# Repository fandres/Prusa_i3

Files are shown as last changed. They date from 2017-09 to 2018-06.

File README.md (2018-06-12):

This repository is possibly outdated
Este Repositorio se probablemente se encuentra desactualizado

Repository migrated to https://gitlab.com/fandres323/Prusa_i3
Repositorio migrado a https://gitlab.com/fandres323/Prusa_i3

# Prusa_i3
============

License 
======

[Creative Commons Attribution-ShareAlike 4.0 International License](http://creativecommons.org/licenses/by-sa/4.0/)

Attributions
============
See commit details to find the authors of each Part.
- @fandres

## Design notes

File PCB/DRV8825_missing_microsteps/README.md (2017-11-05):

## DRV8825 Missing Microsteps
DRV8825 Missing Steps

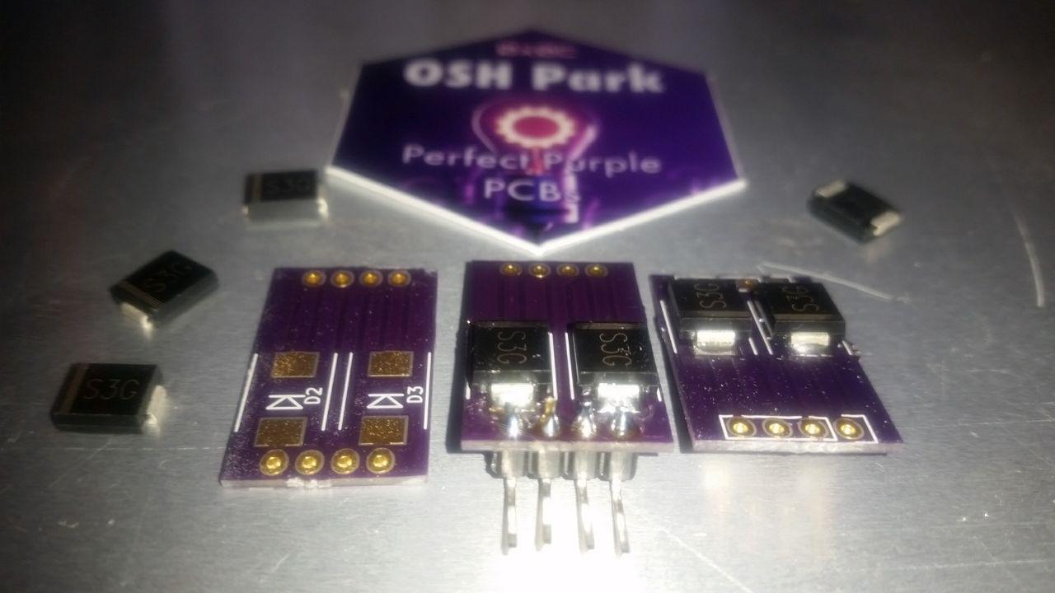
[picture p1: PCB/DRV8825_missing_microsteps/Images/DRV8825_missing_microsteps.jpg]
DRV8825_missing_microsteps


## BOM 
Ref | Qty | Value | Footprint 
--- | --- | ----- | --------
D1 D2 D3 D4  | 4 | S3G SMC DO-214AB 
J1 J2  | 2 | Conn_01x04 

# Order from OSH Park, $3 x2.85 



# Images
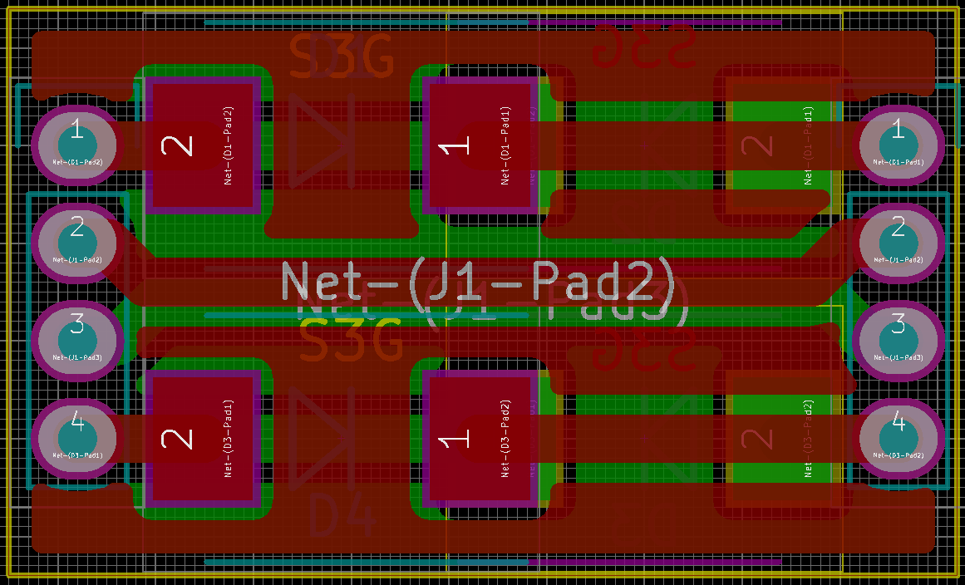
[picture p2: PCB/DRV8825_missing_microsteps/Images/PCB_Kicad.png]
PCB_Kicad


# License 
======

[MIT License](/PCB/DRV8825_missing_microsteps/Images/LICENCE)

# Attributions
============
See commit details to find the authors of each Part.
- @fandres

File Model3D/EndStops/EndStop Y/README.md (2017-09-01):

# Model 3D on FreeCad
============

# Images
3D_

# License 
======

[Creative Commons Attribution-ShareAlike 4.0 International License](http://creativecommons.org/licenses/by-sa/4.0/)

# Attributions
============
Based on the design of by clefranc, Endstop Y Support for Prusa i3 licensed under the Creative Commons - Attribution license. 

See commit details to find the authors of each Part.
- @fandres

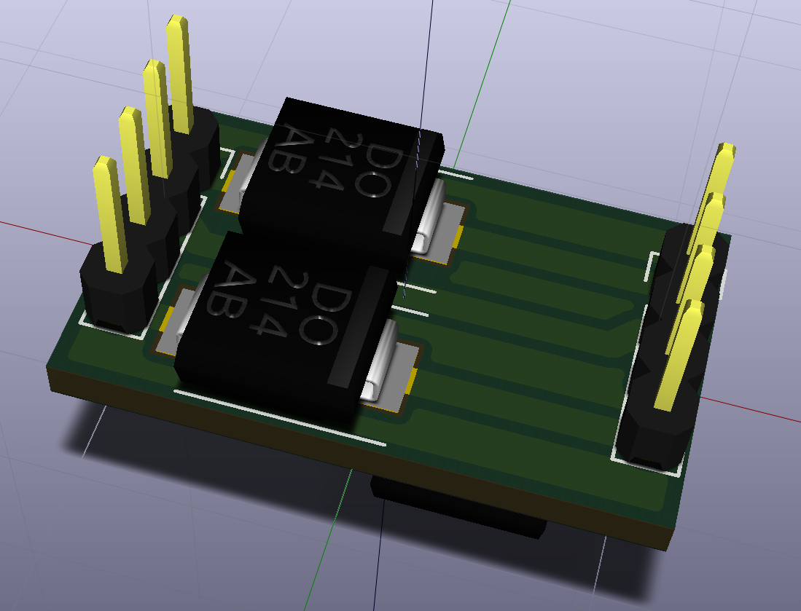
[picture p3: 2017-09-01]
PCB/DRV8825_missing_microsteps/Images/3D_View-F.png

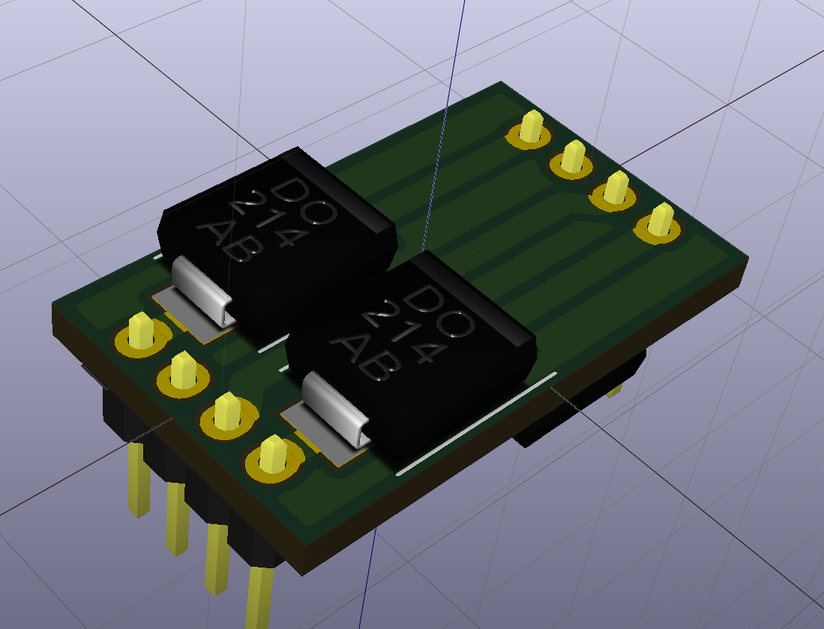
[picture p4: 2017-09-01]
PCB/DRV8825_missing_microsteps/Images/3D_View-B.png

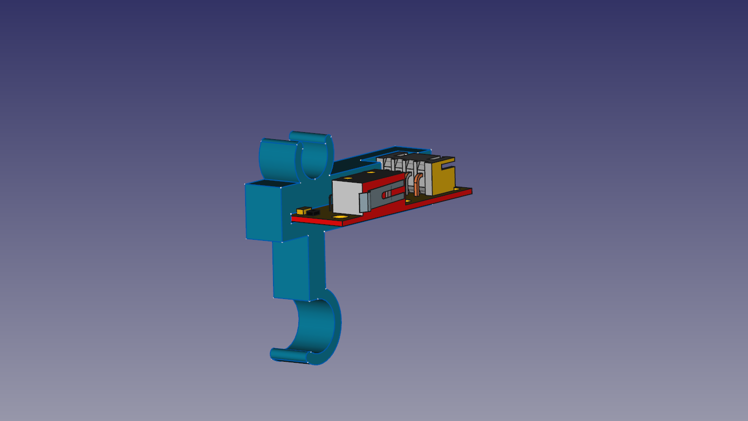
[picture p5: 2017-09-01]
Model3D/EndStops/EndStop Y/Endstop Y.png

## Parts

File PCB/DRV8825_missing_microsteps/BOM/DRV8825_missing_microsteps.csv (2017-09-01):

Title | DRV8825 Missing Microsteps
Revision | 1
Date
Generated | jue 31 ago 2017 22:43:22 -05
Company | Rootdevel
Comment 1 | fAndRes
Comment 2 | CC-4.0 Internacional By
Comment 3
Comment 4
Total Parts | 6
Total Unique Parts | 2
Ref | Qty | Value | Footprint
D1 D2 D3 D4 | 4 | S3G | Diodes_SMD:DO-214AB
J1 J2 | 2 | Conn_01x04 | Pin_Headers:Pin_Header_Straight_1x04
BOM made with KICAD_BOM_WIZARD (https://github.com/HashDefineElectronics/KiCad_BOM_Wizard.git)
Generated jue 31 ago 2017 22:43:22 -05

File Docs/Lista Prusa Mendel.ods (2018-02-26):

 | Estructura |  |  | Electrónica |  | Presupuesto
Cantidad | Elemento |  | Cantidad | Elemento |  | 1.1 | $115.000 | Electrónica básica + DRV8825 Missing
1 | Marco de Aluminio/Acrilico | 4 | 1 | Arduino Mega | 1.1 | 1.2 | $42.000 | Mecánica movimiento
1 | Juego de piezas imprimibles | 5 | 1 | Ramps 1.4 | 1.1 | 2 | $134.100 | Motores
 | Varillas Roscadas | 6 | 1 | HotEnd | 3.1 | 3.1 | $42.000 | Hotend
2 | Métrica 10 (380mm) | 6 | 1 | Cama caliente 200x200mm | 3.3 | 3.2 | $90.000 | Extrusor
4 | Métrica 8 (210mm) | 6 | 5 | Pololu + disipador | 1.1 | 4 | $90.000 | Marco
2 | Métrica 5 (295mm) | 6 | 2 | Termistor de 100K | 3.3 | 5 | $90.000 | Vitaminas + Endstop
 | Varillas Lisas | 6 | 1 | Fuente de alimentación 12v. (al menos de 20A) | 8 | 6 | $80.000 | Estructura: varillas
2 | Métrica 8 (345mm) EJE Y | 6 | 1 | Pantalla LCD (opcional) | 8 | 7 | $109.000 | Tornilleria, Hot-bed y otros
2 | Métrica 8 (320mm) EJE Z | 6 | 3 | Finales de carrera | 5 | 8 | $80.000 | Power Suply + LCD
2 | Métrica 8 (380mm) EJE X | 6 | 3 | Ventilador (electrónica) x2 / x1 Radial | 1.1 | 9 | $83.000 | Filamento
1 | Métrica 8 (20mm) | 6 | 1 | Juego de cableado | 7
 |  |  | 1 | Sensor de proximidad Nivel (Inductivo, BLTouch) | 1.1 |  | Subtotal | 955100
 |  |  | 5 | DRV8825 Missing | 1.1
 | Mecánica
Cantidad | Elemento
5 | Motores NEMA 17 | 2 |  | Tuercas , tornillería y arandelas
2 | Correas GT2 | 1.2 | Cantidad | Elemento
2 | Poleas GT2 | 1.2 |  | Tuercas | 7
10 | Rodamiento LM8UU | 1.2 | 12 | Métrica 10 | 7
2 | Rodamiento 623zz | 1.2 | 24 | Métrica 8 | 7
3 | Rodamiento 608zz | 1.2 | 2 | Métrica 5 | 7
2 | Acoples eje Z | 1.2 | - | Métrica 4 | 7
1 | Tornillo extrusor (hobed bolt) | 3.2 | - | Métrica 3 | 7
4 | Muelle Cama Caliente (20-25mm) | 7 | Cantidad | Tornillería | 7
2 | Muelles Extrusor | 3.2 | - | Métrica 4 (25,50mm) | 7
 | 624zz | 1,2 | - | Métrica 3 (10, 20, 25, 40mm) | 7
 |  |  |  | Arandelas | 7
 |  |  | 8 | Métrica 10 | 7
 | Varios |  | 4 | Métrica 10 de ala ancha (para el marco) | 7
1 | Espejo / Cristal 214x214 | 7 | 24 | Métrica 8 | 7
1 | Cable alimentación | 7 | - | Métrica 4 | 7
1 | Cinta Kapton | 7 | - | Métrica 3 | 7
- | Bridas
1 | Laca
Ref: | https://kitprinter3d.com/es/
 | www.zonamaker.com/tienda/es
Esta obra está licenciada bajo la Licencia Creative Commons Atribución-NoComercial 4.0 Internacional. Para ver una copia de esta licencia, visita http://creativecommons.org/licenses/by-nc/4.0/.

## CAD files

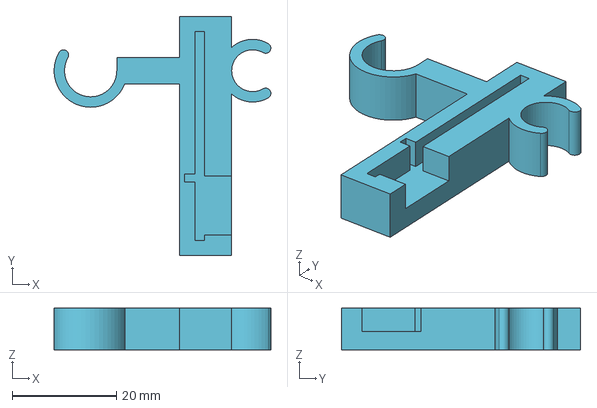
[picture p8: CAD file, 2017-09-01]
Model3D/EndStops/EndStop Y/EndStopY.step
41.5 x 45.8 x 8.00 mm

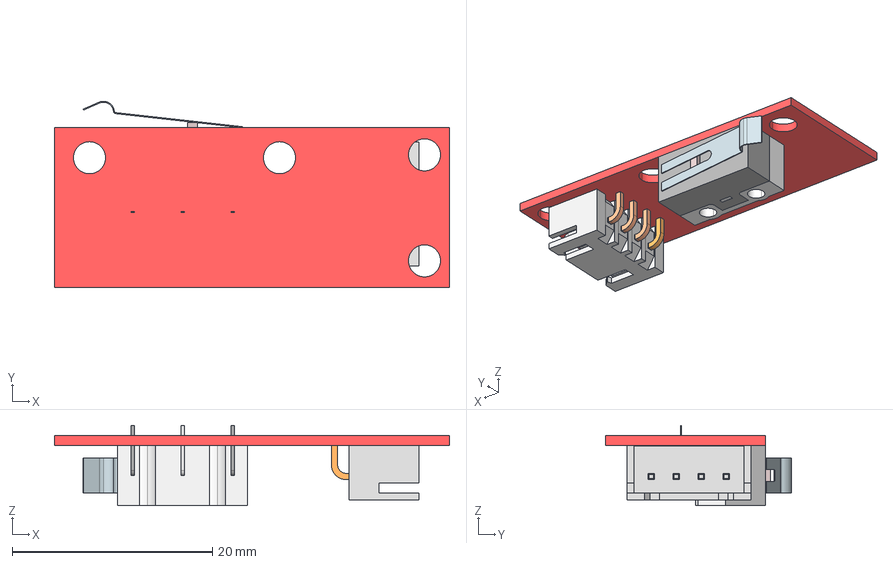
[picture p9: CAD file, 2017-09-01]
Model3D/EndStops/EndStop Y/parts/endstop-by Mirko Arndt /Konstruktion24.stp
39.5 x 18.6 x 8.00 mm
Konstruktion24
PCB^Endstop
Microswitch_1A_125vAC(seul)
JST 4Pin

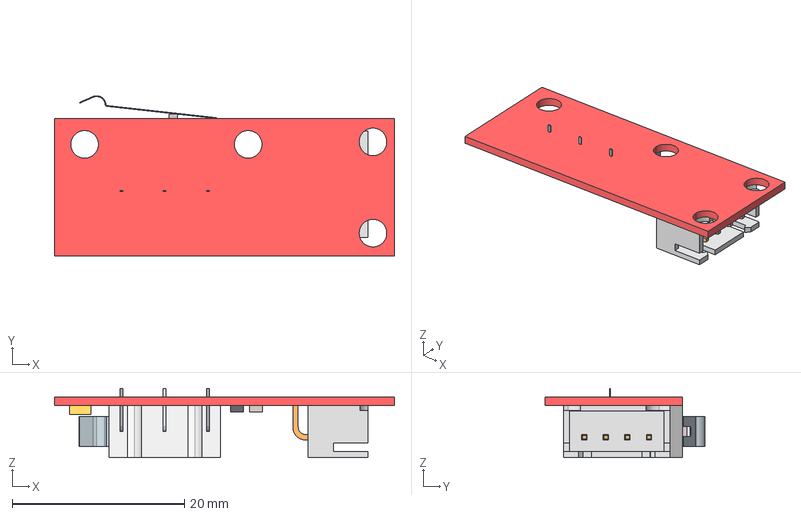
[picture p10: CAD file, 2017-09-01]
Model3D/EndStops/EndStop Y/parts/endstop-by Mirko Arndt /Endstop2.stp
39.5 x 18.6 x 8.02 mm
PCB Geometry
PCB^Endstop
Microswitch_1A_125vAC(seul)
JST 4Pin

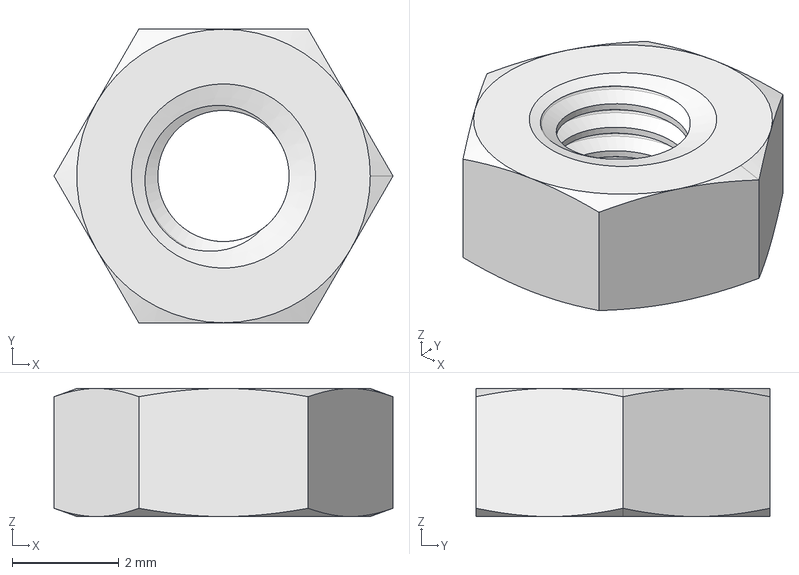
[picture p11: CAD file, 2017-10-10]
Model3D/Fasteners/tuerca_seguridad/tuerca_seguridad.step
6.35 x 5.50 x 2.40 mm

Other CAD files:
Model3D/EndStops/EndStop Y/EndStopY.stl
Model3D/EndStops/EndStop Y/Endstop Y.fcstd
Model3D/EndStops/EndStop Y/parts/endstop-by Mirko Arndt /Konstruktion24.igs
Model3D/Fasteners/tuerca_seguridad/tuerca_seguridad.fcstd
Model3D/Fasteners/tuerca_seguridad/tuerca_seguridad.stl

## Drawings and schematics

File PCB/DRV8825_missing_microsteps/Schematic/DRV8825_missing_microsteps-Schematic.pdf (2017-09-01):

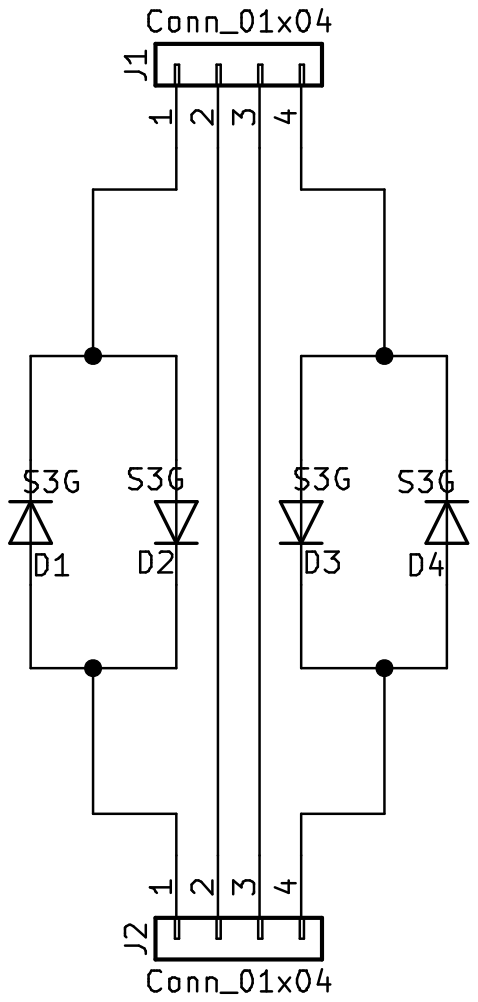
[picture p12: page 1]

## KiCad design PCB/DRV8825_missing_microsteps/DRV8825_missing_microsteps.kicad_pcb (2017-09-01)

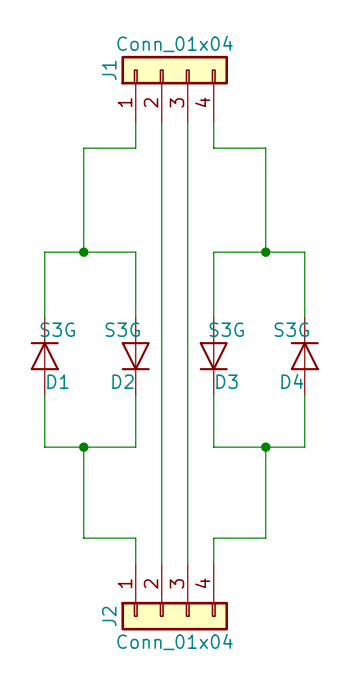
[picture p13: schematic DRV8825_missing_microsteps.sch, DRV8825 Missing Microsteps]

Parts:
D1, D2, D3, D4: S3G; DO-214AB
J1, J2: Conn_01x04; Pin_Header_Straight_1x04

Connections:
unnamed: D1.1 (K), D2.2 (A), J1.1
unnamed: D1.2 (A), D2.1 (K), J2.1
unnamed: D3.1 (K), D4.2 (A), J2.4
unnamed: D3.2 (A), D4.1 (K), J1.4
unnamed: J1.2, J2.2
unnamed: J1.3, J2.3

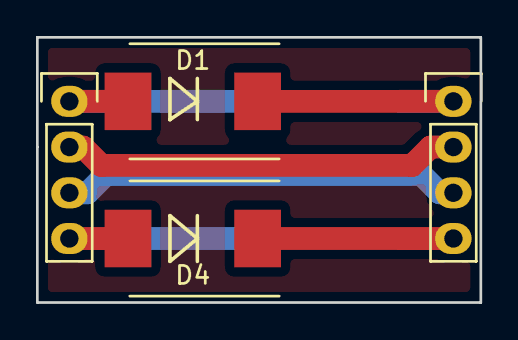
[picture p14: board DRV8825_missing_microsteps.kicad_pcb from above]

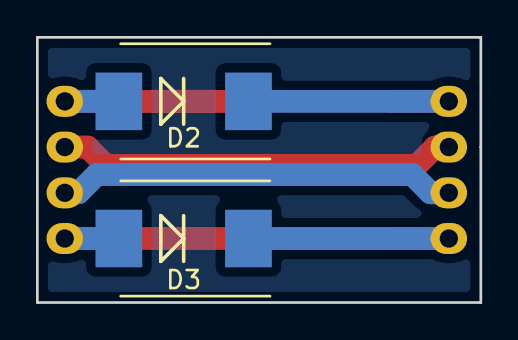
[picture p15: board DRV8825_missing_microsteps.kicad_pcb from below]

Board: 2 copper layers, 24.6 x 14.7 mm, 6 parts (2 on the bottom side), 6 nets.

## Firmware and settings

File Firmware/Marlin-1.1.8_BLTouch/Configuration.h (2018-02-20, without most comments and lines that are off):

#include <U8glib.h>
#define CONFIGURATION_H
#define CONFIGURATION_H_VERSION 010107
#define STRING_CONFIG_H_AUTHOR "(none, default config)" // Who made the changes.
#define SHOW_BOOTSCREEN
#define STRING_SPLASH_LINE1 SHORT_BUILD_VERSION // will be shown during bootup in line 1
#define STRING_SPLASH_LINE2 WEBSITE_URL         // will be shown during bootup in line 2
#define SERIAL_PORT 0
#define BAUDRATE 250000
  #define MOTHERBOARD BOARD_RAMPS_14_EFB
#define EXTRUDERS 1
#define DEFAULT_NOMINAL_FILAMENT_DIA 1.75
#define POWER_SUPPLY 0
#define TEMP_SENSOR_0 60
#define TEMP_SENSOR_1 0
#define TEMP_SENSOR_2 0
#define TEMP_SENSOR_3 0
#define TEMP_SENSOR_4 0
#define TEMP_SENSOR_BED 60
#define DUMMY_THERMISTOR_998_VALUE 25
#define DUMMY_THERMISTOR_999_VALUE 100
#define MAX_REDUNDANT_TEMP_SENSOR_DIFF 10
#define TEMP_RESIDENCY_TIME 10  // (seconds)
#define TEMP_HYSTERESIS 3       // (degC) range of +/- temperatures considered "close" to the target one
#define TEMP_WINDOW     1       // (degC) Window around target to start the residency timer x degC early.
#define TEMP_BED_RESIDENCY_TIME 10  // (seconds)
#define TEMP_BED_HYSTERESIS 3       // (degC) range of +/- temperatures considered "close" to the target one
#define TEMP_BED_WINDOW     1       // (degC) Window around target to start the residency timer x degC early.
#define HEATER_0_MINTEMP 5
#define HEATER_1_MINTEMP 5
#define HEATER_2_MINTEMP 5
#define HEATER_3_MINTEMP 5
#define HEATER_4_MINTEMP 5
#define BED_MINTEMP 5
#define HEATER_0_MAXTEMP 290
#define HEATER_1_MAXTEMP 275
#define HEATER_2_MAXTEMP 275
#define HEATER_3_MAXTEMP 275
#define HEATER_4_MAXTEMP 275
#define BED_MAXTEMP 150
#define PIDTEMP
#define BANG_MAX 255     // Limits current to nozzle while in bang-bang mode; 255=full current
#define PID_MAX BANG_MAX // Limits current to nozzle while PID is active (see PID_FUNCTIONAL_RANGE below); 255=full current
#define PID_K1 0.95      // Smoothing factor within the PID
  #define PID_FUNCTIONAL_RANGE 10 // If the temperature difference between the target temperature and the actual temperature
  #define  DEFAULT_Kp 20.51
  #define  DEFAULT_Ki 1.76
  #define  DEFAULT_Kd 59.65
#define PIDTEMPBED
#define MAX_BED_POWER 255 // limits duty cycle to bed; 255=full current
  #define  DEFAULT_bedKp 1120.44
  #define  DEFAULT_bedKi 184.33
  #define  DEFAULT_bedKd 1698.03
#define PREVENT_COLD_EXTRUSION
#define EXTRUDE_MINTEMP 170
#define PREVENT_LENGTHY_EXTRUDE
#define EXTRUDE_MAXLENGTH 200
#define THERMAL_PROTECTION_HOTENDS // Enable thermal protection for all extruders
#define THERMAL_PROTECTION_BED     // Enable thermal protection for the heated bed
#define USE_XMIN_PLUG
#define USE_YMIN_PLUG
#define USE_ZMIN_PLUG
#define ENDSTOPPULLUPS // Comment this out (using // at the start of the line) to disable the endstop pullup resistors
#define X_MIN_ENDSTOP_INVERTING true // set to true to invert the logic of the endstop.
#define Y_MIN_ENDSTOP_INVERTING true // set to true to invert the logic of the endstop.
#define Z_MIN_ENDSTOP_INVERTING false // set to true to invert the logic of the endstop.
#define X_MAX_ENDSTOP_INVERTING false // set to true to invert the logic of the endstop.
#define Y_MAX_ENDSTOP_INVERTING false // set to true to invert the logic of the endstop.
#define Z_MAX_ENDSTOP_INVERTING false // set to true to invert the logic of the endstop.
#define Z_MIN_PROBE_ENDSTOP_INVERTING false // set to true to invert the logic of the probe.
#define DEFAULT_AXIS_STEPS_PER_UNIT   { 160, 160, 8000, 896 } //{ 80, 80, 4000, 500 } 8000 = (200pasos/1mm)*32 | (200/20_dientes)*32 ; Extrusor Titan -> Steps per Unit (Extruder) = Motor Steps * Micro-stepping * Gear Ratio / (Hobb Diameter * Pi) = (200*32*3)/(7.3*3.1412) = 837,3032555397204
#define DEFAULT_MAX_FEEDRATE          { 300, 300, 3, 25 }  // { 300, 300, 5, 25 }
#define DEFAULT_MAX_ACCELERATION      { 3000, 3000, 50, 10000 }  // { 3000, 3000, 100, 10000 }
#define DEFAULT_ACCELERATION          3000    // X, Y, Z and E acceleration for printing moves
#define DEFAULT_RETRACT_ACCELERATION  3000    // E acceleration for retracts
#define DEFAULT_TRAVEL_ACCELERATION   3000    // X, Y, Z acceleration for travel (non printing) moves
#define DEFAULT_XJERK                 10.0
#define DEFAULT_YJERK                 10.0
#define DEFAULT_ZJERK                  0.3
#define DEFAULT_EJERK                  5.0
#define Z_MIN_PROBE_USES_Z_MIN_ENDSTOP_PIN
#define Z_SERVO_ANGLES {10,90}  // Z Servo Deploy and Stow angles  /// 70,0
#define BLTOUCH
#define X_PROBE_OFFSET_FROM_EXTRUDER -3  // X offset: -left  +right  [of the nozzle]
#define Y_PROBE_OFFSET_FROM_EXTRUDER 3  // Y offset: -front +behind [the nozzle]
#define Z_PROBE_OFFSET_FROM_EXTRUDER -1.9   // Z offset: -below +above  [the nozzle]
#define XY_PROBE_SPEED 8000
#define Z_PROBE_SPEED_FAST HOMING_FEEDRATE_Z
#define Z_PROBE_SPEED_SLOW (Z_PROBE_SPEED_FAST / 2)
#define Z_CLEARANCE_DEPLOY_PROBE   10 // Z Clearance for Deploy/Stow
#define Z_CLEARANCE_BETWEEN_PROBES  5 // Z Clearance between probe points
#define Z_PROBE_OFFSET_RANGE_MIN -20
#define Z_PROBE_OFFSET_RANGE_MAX 20
#define X_ENABLE_ON 0
#define Y_ENABLE_ON 0
#define Z_ENABLE_ON 0
#define E_ENABLE_ON 0 // For all extruders
#define DISABLE_X false
#define DISABLE_Y false
#define DISABLE_Z false
#define DISABLE_E false // For all extruders
#define DISABLE_INACTIVE_EXTRUDER true // Keep only the active extruder enabled.
#define INVERT_X_DIR false
#define INVERT_Y_DIR true
#define INVERT_Z_DIR false
#define INVERT_E0_DIR false
#define INVERT_E1_DIR false
#define INVERT_E2_DIR false
#define INVERT_E3_DIR false
#define INVERT_E4_DIR false
#define X_HOME_DIR -1
#define Y_HOME_DIR -1
#define Z_HOME_DIR -1
#define X_BED_SIZE 190 //200
#define Y_BED_SIZE 180 //200
#define X_MIN_POS 0
#define Y_MIN_POS 0
#define Z_MIN_POS 0
#define X_MAX_POS X_BED_SIZE
#define Y_MAX_POS Y_BED_SIZE
#define Z_MAX_POS 138  //200
#define MAX_SOFTWARE_ENDSTOPS
  #define MAX_SOFTWARE_ENDSTOP_X
  #define MAX_SOFTWARE_ENDSTOP_Y
  #define MAX_SOFTWARE_ENDSTOP_Z
#define AUTO_BED_LEVELING_3POINT
  #define ABL_PROBE_PT_1_X 15 //15
  #define ABL_PROBE_PT_1_Y 170 //180
  #define ABL_PROBE_PT_2_X 185 //15
  #define ABL_PROBE_PT_2_Y 100  //50 = 20 seguro + 37 offset extruder
  #define ABL_PROBE_PT_3_X 185 // 170
  #define ABL_PROBE_PT_3_Y 180 //50 = 20 seguro + 37 offset extruder
#define Z_SAFE_HOMING
  #define Z_SAFE_HOMING_X_POINT ((X_BED_SIZE) / 2)    // X point for Z homing when homing all axes (G28).
  #define Z_SAFE_HOMING_Y_POINT ((Y_BED_SIZE) / 2)    // Y point for Z homing when homing all axes (G28).
#define HOMING_FEEDRATE_XY (50*60)
#define HOMING_FEEDRATE_Z  (4*60)
#define EEPROM_SETTINGS // Enable for M500 and M501 commands
#define EEPROM_CHITCHAT   // Give feedback on EEPROM commands. Disable to save PROGMEM.
#define HOST_KEEPALIVE_FEATURE        // Disable this if your host doesn't like keepalive messages
#define DEFAULT_KEEPALIVE_INTERVAL 2  // Number of seconds between "busy" messages. Set with M113.
#define BUSY_WHILE_HEATING            // Some hosts require "busy" messages even during heating
#define PREHEAT_1_TEMP_HOTEND 160 //180
#define PREHEAT_1_TEMP_BED     68 //70
#define PREHEAT_1_FAN_SPEED     0 // Value from 0 to 255
#define PREHEAT_2_TEMP_HOTEND 240
#define PREHEAT_2_TEMP_BED    110
#define PREHEAT_2_FAN_SPEED     0 // Value from 0 to 255
#define PRINTJOB_TIMER_AUTOSTART
#define LCD_LANGUAGE es
#define DISPLAY_CHARSET_HD44780 JAPANESE
#define SDSUPPORT
#define REPRAP_DISCOUNT_FULL_GRAPHIC_SMART_CONTROLLER
#define SOFT_PWM_SCALE 0
#define NUM_SERVOS 1 // Servo index starts with 0 for M280 command
#define SERVO_DELAY { 300 }

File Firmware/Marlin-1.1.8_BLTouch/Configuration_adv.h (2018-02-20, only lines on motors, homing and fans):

#define E0_AUTO_FAN_PIN -1
#define E1_AUTO_FAN_PIN -1
#define E2_AUTO_FAN_PIN -1
#define E3_AUTO_FAN_PIN -1
#define E4_AUTO_FAN_PIN -1
#define X_HOME_BUMP_MM 5
#define Y_HOME_BUMP_MM 5
#define Z_HOME_BUMP_MM 5  ///2
#define HOMING_BUMP_DIVISOR { 2, 2, 4 }  // Re-Bump Speed Divisor (Divides the Homing Feedrate)
#define MICROSTEP_MODES {16,16,16,16,16} // [1,2,4,8,16]
#define DIGIPOT_I2C_MOTOR_CURRENTS { 1.0, 1.0, 1.0, 1.0, 1.0, 1.0, 1.0, 1.0 }  //  AZTEEG_X3_PRO

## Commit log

2017-09-01 Model Endstop Y
    [EndStopY.step, EndStopY.stl, Endstop Y.fcstd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]
2017-09-01 Added Config Firmware Marlin
    [Configuration.h]
2017-09-01 Added list of parts and costs
    [Lista Prusa Mendel.ods]
2017-09-01 PCB: DRV8825 Missing Microsteps
    [DRV8825_missing_microsteps.csv, DRV8825_missing_microsteps.kicad_pcb, DRV8825_missing_microsteps.sch]
2017-09-15 Update Speed Z
    [Configuration.h]
2017-10-06 Autotuning Bed And Hotend
    [Configuration.h]
2017-10-10 Ajusts 3Points Added SD Card
    [Configuration.h]
2017-10-10 Fork Marlin 1.1.6
    [Configuration.h]
2017-10-10 Fasteners security: BED
    [tuerca_seguridad.fcstd, tuerca_seguridad.step, tuerca_seguridad.stl]
2017-12-27 Update config Marlin firmware 1.1.7
    [Configuration.h]
2018-01-29 Added firmware marlin 1.1.8
    [Configuration.h]
2018-02-20 Added Config for BLTouch
    [Configuration.h, Configuration_adv.h]
2018-02-26 Added Components: BLTOuch, DRV8825 missing and others
    [Lista Prusa Mendel.ods]

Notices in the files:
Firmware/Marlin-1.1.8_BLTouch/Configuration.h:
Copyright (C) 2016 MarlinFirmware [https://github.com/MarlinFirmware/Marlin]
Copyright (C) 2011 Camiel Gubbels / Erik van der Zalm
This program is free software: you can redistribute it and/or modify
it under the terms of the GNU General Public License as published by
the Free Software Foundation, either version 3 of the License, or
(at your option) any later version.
